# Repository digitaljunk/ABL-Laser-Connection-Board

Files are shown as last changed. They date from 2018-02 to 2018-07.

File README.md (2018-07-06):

# ABL-Laser-Connection-Board
https://www.thingiverse.com/thing:2757972

This circuit board provides ABL and Laser functionally trough a 6 wire cable to the print head. It's designed for laser modules with separate 5V PWM and 12V work voltage

It also brings down the 12V PWM signal from the part cooling fan to 5V PWM to
connect the laser module PWM/TTL port.
It provides a 12V work voltage with the ability to add a safety switch to prevent laser operation during printer start up. You can also add door switches or an emergency switch so secure the laser operation.
You can optionally connect an external power supply for the laser and ABL sensor.
The board provides an optocoupler for the ABL sensor.
All connections are provided via an 6-pin connector to the print head.

You can mount the PCB to the printer frame with 3mm bolds and headnuts near the Z stepper.

Feel free to provide a nice and snugly printable case. You can bend the LED to point upwards the PCB.

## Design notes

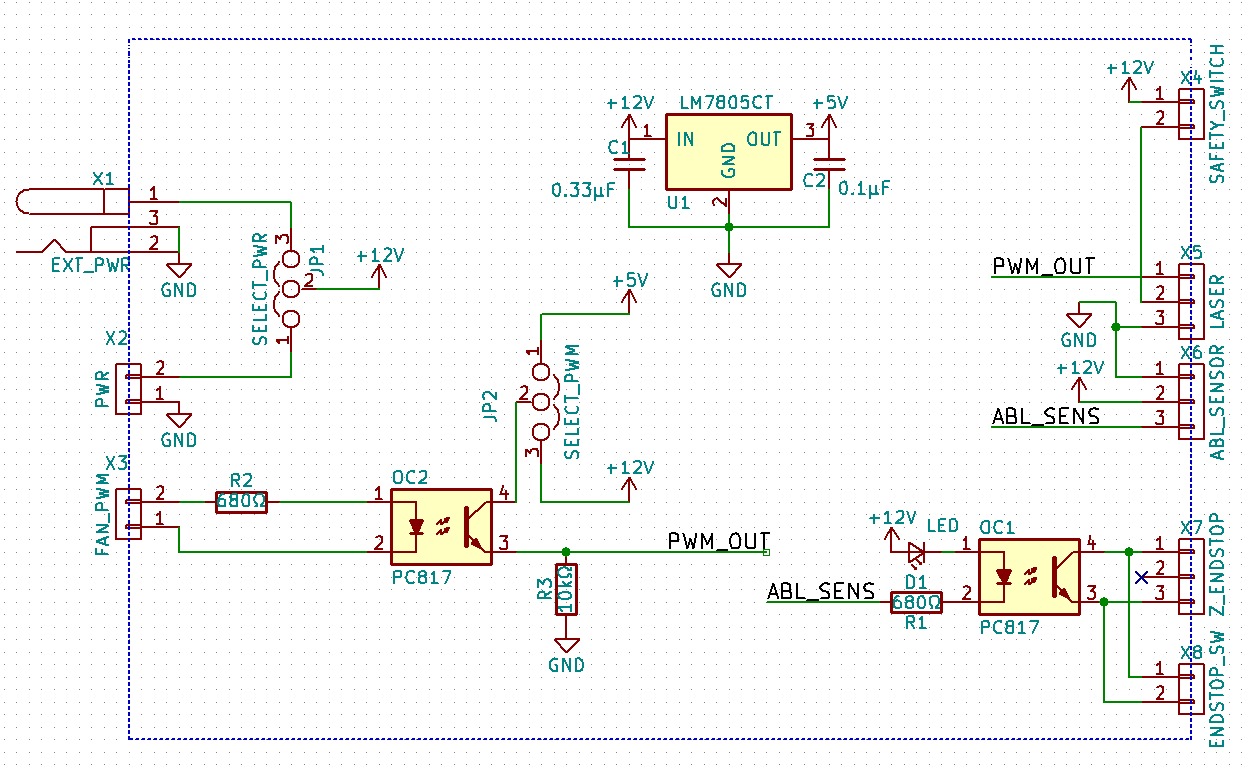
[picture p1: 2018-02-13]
img/ee99d8bf-4e51-4896-a9b2-5014b873ce79.jpg

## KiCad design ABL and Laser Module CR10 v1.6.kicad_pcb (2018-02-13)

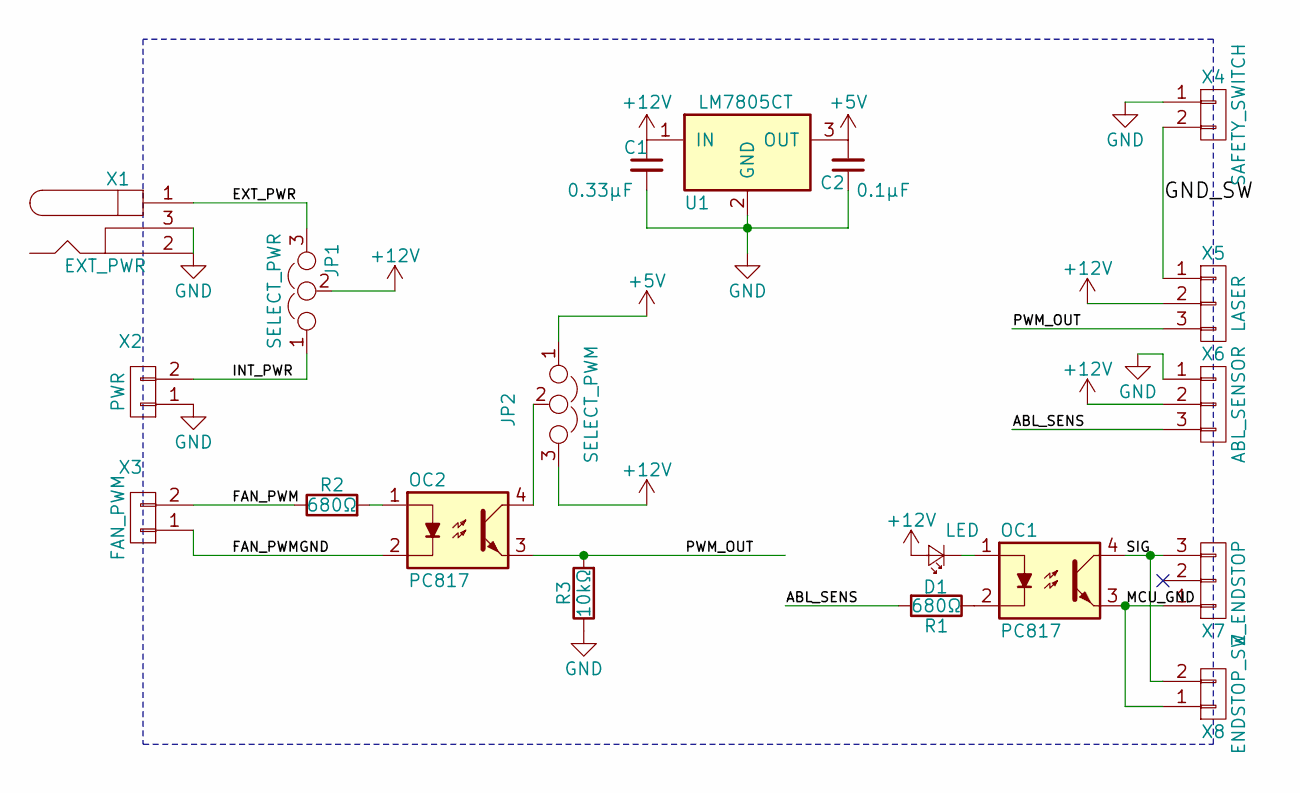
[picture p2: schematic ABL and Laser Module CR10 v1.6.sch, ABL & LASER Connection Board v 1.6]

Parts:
C1: 0.33µF; C_Disc_D5.0mm_W2.5mm_P5.00mm
C2: 0.1µF; C_Disc_D5.0mm_W2.5mm_P5.00mm
D1: LED; LED_D3.0mm
JP1: SELECT_PWR; Pin_Header_Straight_1x03_Pitch2.54mm
JP2: SELECT_PWM; Pin_Header_Straight_1x03_Pitch2.54mm
OC1, OC2: PC817; DIP-4_W7.62mm
R1, R2: 680Ω; R_Axial_DIN0207_L6.3mm_D2.5mm_P7.62mm_Horizontal
R3: 10kΩ; R_Axial_DIN0207_L6.3mm_D2.5mm_P7.62mm_Horizontal
U1: LM7805CT; TO-220-3_Horizontal_thermal
X1: EXT_PWR; Barrel_Jack_CUI_PJ-102AH
X2: PWR; JST_XH_S02B-XH-A_02x2.50mm_Angled
X3: FAN_PWM; JST_XH_S02B-XH-A_02x2.50mm_Angled
X4: SAFETY_SWITCH; JST_XH_S02B-XH-A_02x2.50mm_Angled
X5: LASER; JST_XH_S03B-XH-A_03x2.50mm_Angled
X6: ABL_SENSOR; JST_XH_S03B-XH-A_03x2.50mm_Angled
X7: Z_ENDSTOP; JST_XH_S03B-XH-A_03x2.50mm_Angled
X8: ENDSTOP_SW; JST_XH_S02B-XH-A_02x2.50mm_Angled

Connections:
+5V: C2.2, JP2.1, U1.3 (OUT)
+12V: C1.1, D1.2 (A), JP1.2, JP2.3, U1.1 (IN), X5.2, X6.2
/ABL_SENS: R1.2, X6.3
/EXT_PWR: JP1.3, X1.1
/FAN_PWM: R2.1, X3.2
/FAN_PWMGND: OC2.2, X3.1
/GND_SW: X4.2, X5.1
/INT_PWR: JP1.1, X2.2
/MCU_GND: OC1.3, X7.1, X8.1
/PWM_OUT: OC2.3, R3.2, X5.3
/SIG: OC1.4, X7.3, X8.2
GND: C1.2, C2.1, R3.1, U1.2 (GND), X1.2, X1.3, X2.1, X4.1, X6.1
unnamed: D1.1 (K), OC1.1
unnamed: JP2.2, OC2.4
unnamed: OC1.2, R1.1
unnamed: OC2.1, R2.2

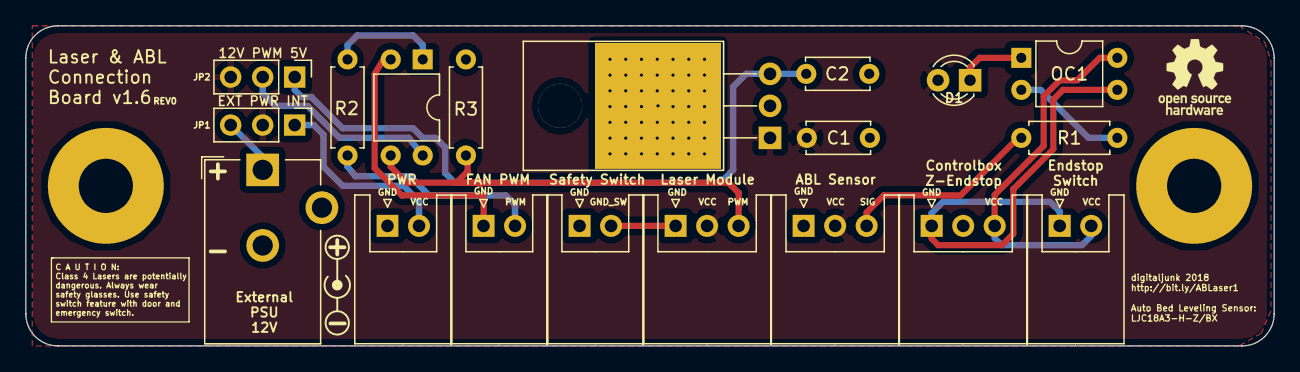
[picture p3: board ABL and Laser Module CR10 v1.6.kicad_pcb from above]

Board: 2 copper layers, 99.1 x 25.4 mm, 19 parts (0 on the bottom side), 16 nets.
